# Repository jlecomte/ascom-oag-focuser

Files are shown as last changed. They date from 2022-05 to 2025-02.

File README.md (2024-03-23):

# ASCOM-Compatible OAG Focuser

I do not charge anything to create and maintain these open-source projects. But if you would like to say "thanks" for this project, feel free to send any amount through Paypal using the button below. I appreciate your support!

(https://www.paypal.com/donate/?hosted_button_id=49UXY8F6VVYFA)

<!-- toc -->

- [Introduction](#introduction)
  * [Is This For You?](#is-this-for-you)
  * [Use As A Standalone Focuser](#use-as-a-standalone-focuser)
- [Finished Product](#finished-product)
- [Demo](#demo)
- [Pre-Requisites](#pre-requisites)
- [Hardware / BOM](#hardware--bom)
- [ASCOM Driver](#ascom-driver)
  * [Downloading And Installing The Driver](#downloading-and-installing-the-driver)
  * [Compiling The Driver (For Developers Only)](#compiling-the-driver-for-developers-only)
  * [Screenshots](#screenshots)
- [Standalone Focuser Application](#standalone-focuser-application)
- [Arduino Firmware](#arduino-firmware)
  * [Microcontroller Compatibility](#microcontroller-compatibility)
  * [Compiling And Uploading The Firmware](#compiling-and-uploading-the-firmware)
- [Electronic Circuit](#electronic-circuit)
- [Mechanical Components](#mechanical-components)
  * [OAG Compatibility](#oag-compatibility)
  * [Gear And Pinion](#gear-and-pinion)
- [Calibration Procedure](#calibration-procedure)
- [Troubleshooting](#troubleshooting)
- [Frequently Asked Questions (FAQ)](#frequently-asked-questions-faq)
- [Credits](#credits)

<!-- tocstop -->

## Introduction

Shortly after I got started in astrophotography, I noticed that the stars in my images were slightly elongated due to some differential flexure somewhere in my imaging system (see [Cloudy Nights thread](https://www.cloudynights.com/topic/775260-good-guiding-but-elongated-stars-along-e-w-direction/) — I strongly suspect that it is sag in my focuser...) The permanent solution was to switch from using a guide scope to using an off-axis guider (OAG) and that immediately resolved my issue. Now, my stars are perfectly round, which is great! For reference, I purchased the [ZWO OAG](https://astronomy-imaging-camera.com/product/zwo-oag) and the accompanying [ZWO 1.25" helical focuser](https://astronomy-imaging-camera.com/product/zwo-1-25%E2%80%B3-helical-focuser).

As good as this sounds, the OAG brought a number of new challenges which I did not have to deal with before. First, when using an OAG, the field of view is very small, which sometimes makes it difficult for the guiding software to detect guide stars. Second, the OAG requires some amount of refocusing when switching filters. Indeed, filters are not always parfocal. Most importantly, a refractor (even an apochromatic triplet...) will focus various wavelengths at different distances, and this is the primary reason why it is required to change the focus of the main imaging camera (using filter offsets) when changing filters. Unfortunately, while the imaging sensor is located _behind_ the filter wheel, the OAG is always placed _before_ the filter wheel (Otherwise, especially when using narrowband filters, you would not be able to find a single guide star... Also, placing the filter wheel further away from the imaging sensor would cause vignetting...) and this is why, under specific conditions (see "Is this For You" paragraph below), the guide camera might show out-of-focus images while the imaging camera is in focus, and even though the guide camera was independently focused while another filter was selected in the filter wheel.

While guiding software like PHD2 can accommodate slightly out-of-focus guide stars by computing their centroid, out-of-focus guide images can contain a drastically lower number of detected guide stars, and those that are detected will have a much lower Signal to Noise Ratio (SNR), further reducing the accuracy of the centroid computation. In some situations, PHD2 may not even be able to detect a single guide star, and guiding will be impossible. This has happened to me in the past, and I was forced to _manually_ refocus the guide camera (independently of the main imaging camera of course, using the OAG helical focuser)

Manually refocusing the guide camera throughout the night is not exactly one of the most enjoyable parts of the hobby, so I looked for ways to automate that. Pegasus Astro sells a motorized OAG named [SCOPS OAG](https://pegasusastro.com/products/scops-oag/). However, it is a little expensive for me ($750 US — although it is a really great looking unit!) Furthermore, I discussed with the [N.I.N.A.](https://nighttime-imaging.eu/) developers on their [Discord server](https://discord.gg/fwpmHU4). Since N.I.N.A. can only connect to a single focuser at a time, there is no good solution yet to deal with SCOPS OAG. It is certainly possible to run a second instance of N.I.N.A. that connects to both SCOPS OAG and the guide camera, but there is no way to have those two N.I.N.A. instances communicate to do something upon filter change.

All of this has led me to design and build my own solution to this problem. In this repository, you will find everything you need to motorize and automatically control the ZWO OAG (list of parts, 3D model, electronic schematics, Arduino firmware, ASCOM driver, standalone ASCOM client application, instructions, etc.) I hope you consider building this project if you find yourself in a similar situation. Please note that the ASCOM driver can be used with SCOPS OAG, there is nothing in the Filter Wheel Proxy implementation that is specific to my device.

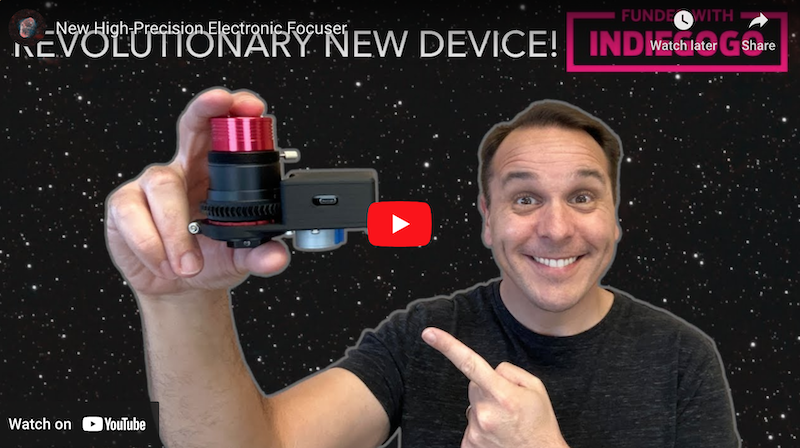
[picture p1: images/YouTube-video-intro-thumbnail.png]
YouTube Intro Video (https://www.youtube.com/watch?v=GP4CpIjJSqA)


### Is This For You?

Not necessarily! It really depends on a lot of factors. For example, if you are using a mirrored telescope, i.e. not a refractor, and if all of your filters come from the same set, e.g., Antlia LRGB filter set, and the filter manufacturer claims they are parfocal, then you may not need this at all because the difference in focus between filters will be so minuscule, you probably won't need to worry about it. However, if you are using a refractor (even an APO triplet), or if you use filters that are not parfocal, you _may_ need this. The only way to find out is to focus your main imaging camera, and then, assuming that you've already defined your filter offsets, go through every single filter in your filter wheel. After every filter change, your imaging application will adjust the focus of your imaging train slightly depending on the filter offset you have defined for the selected filter, and you should look at the image coming out of your guide camera in PHD2. In my case, the stars in my guide camera can be pinpoint when I am using my Luminance filter, but they are large disks when I am on some other filter. That is how you know that this device can be useful for you. This definitely is not for everybody, but the people who have the problem I just described did not really have a good solution until now.

### Use As A Standalone Focuser

Please note that you can use this device, and the accompanying software, to motorize any helical focuser, regardless of how you use that focuser. For example, you could use it to control the focus of a guide scope or even an entire imaging train! Some people have used this project to motorize the focus of a spectrograph. Just remember that if you have a helical focuser that is not from ZWO, you may need to make a few adjustments to the 3D model...

## Finished Product

Here is what the finished product looks like:

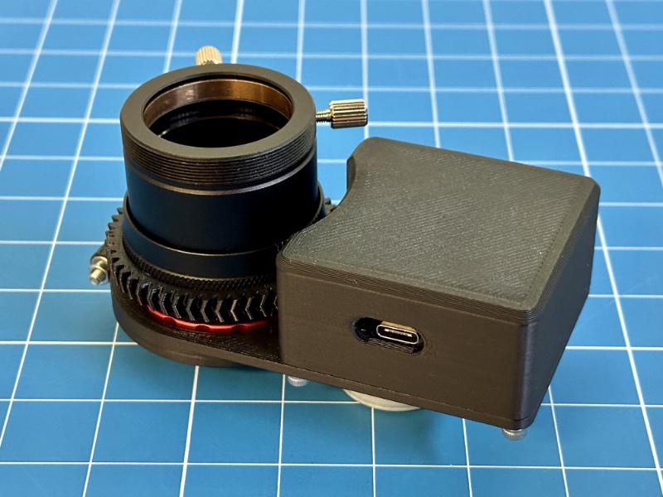
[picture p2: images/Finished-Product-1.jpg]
Finished Product


And here it is, attached to the ZWO OAG, and fitted with a guide camera:

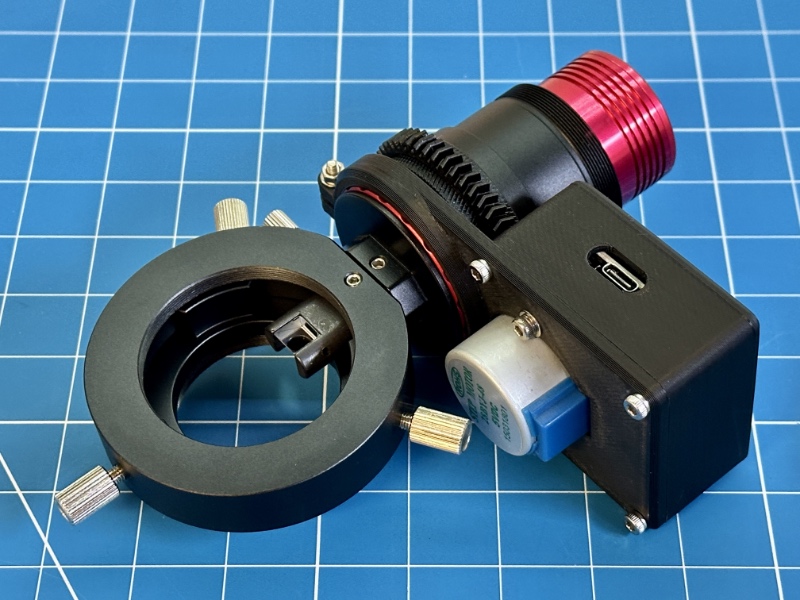
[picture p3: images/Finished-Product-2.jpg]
Finished Product


## Demo

Here is a demo of the system when attached to my telescope, and used as an OAG focuser:

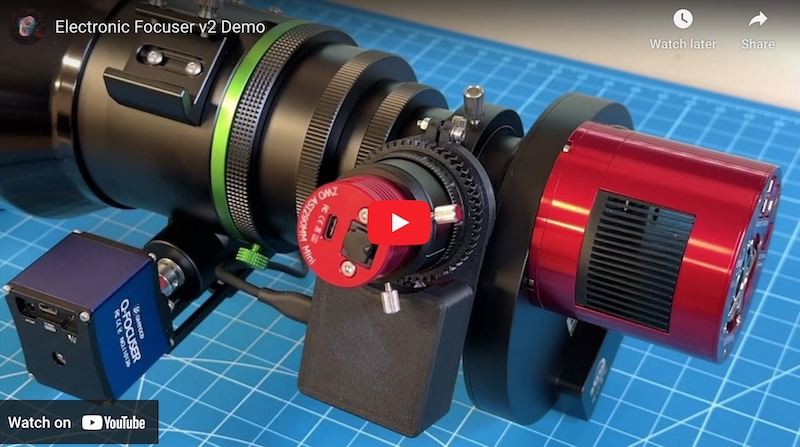
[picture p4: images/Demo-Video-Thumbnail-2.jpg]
YouTube video showing the focuser in action (https://youtu.be/1_InWRwgoRc)


The following video shows what the guide camera sees with and without the OAG focuser upon switching to a different filter:

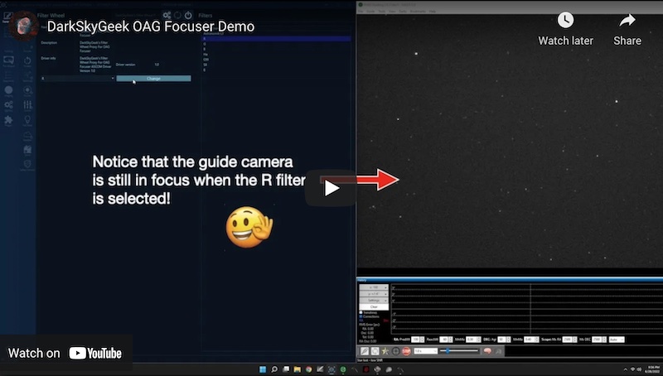
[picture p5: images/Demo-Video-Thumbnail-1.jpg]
YouTube video showing what the guide camera sees with and without an OAG focuser (https://youtu.be/gUapuzT75Z0)


## Pre-Requisites

* A Windows computer (Windows 10 or newer)
* [Microsoft Visual Studio](https://visualstudio.microsoft.com/) (FYI, I used the 2022 edition...)
* [ASCOM Platform](https://ascom-standards.org/)
* [ASCOM Platform Developer Components](https://ascom-standards.org/COMDeveloper/Index.htm)
* [Arduino IDE](https://www.arduino.cc/en/software)
* [FreeCAD](https://www.freecadweb.org/), a free and open-source 3D parametric modeler
* A 3D printer able to print PETG, and a slicer (I use a heavily upgraded Creality Ender 3 v2, and Ultimaker Cura)
* A few basic tools that any tinkerer must own, such as a breadboard, a soldering iron, etc.

## Hardware / BOM

* [ZWO 1.25" helical focuser](https://bit.ly/47JOTRL) or equivalent.
* Arduino-compatible microcontroller board with built-in EEPROM support. I used an [Arduino Nano clone with a USB-C connector (~$10 USD on Amazon for a pack of 3...)](https://www.amazon.com/dp/B09DKHWSY9?tag=darkskygeek-20)
* [ULN2003 Darlington transistor array](https://www.amazon.com/dp/B0CBM23ZJ3?tag=darkskygeek-20) to control the stepper motor using the Arduino's digital I/O pins.
* [28BYJ-48 stepper motor (5V)](https://www.amazon.com/dp/B01CP18J4A?tag=darkskygeek-20)
* [LEDs](https://www.amazon.com/dp/B09XDMJ6KY?tag=darkskygeek-20) and [resistors](https://www.amazon.com/dp/B08FD1XVL6?tag=darkskygeek-20) — These are not required, but they can be useful to debug the firmware while prototyping.
* Connectors — I used [JST-XH connectors](https://www.amazon.com/dp/B01MCZE2HM?tag=darkskygeek-20), only because I already had a bunch of them, along with [a crimping tool](https://www.amazon.com/dp/B078WNZ9FW?tag=darkskygeek-20).
* [Capacitors](https://www.amazon.com/dp/B07PBQXQNQ?tag=darkskygeek-20) — Any 10 to 20µF cpacitor should work (this is just a bulk capacitor, so the exact value does not matter)
* [M2 Threaded Inserts](https://www.amazon.com/dp/B0B8GN63S2?tag=darkskygeek-20)
* [M3 Threaded Inserts](https://www.amazon.com/dp/B0BQJ6CRNJ?tag=darkskygeek-20)

## ASCOM Driver

### Downloading And Installing The Driver

Starting with version `1.0.5`, you can install the ASCOM driver, as well as the standalone focuser control application, by running the executable setup file that you will find in the [releases page](https://github.com/jlecomte/ascom-oag-focuser/releases). By default, it places files under `C:\Program Files (x86)\Dark Sky Geek\OAG Focuser ASCOM Driver`.

### Compiling The Driver (For Developers Only)

Open Microsoft Visual Studio as an administrator (right-click on the Microsoft Visual Studio shortcut, and select "Run as administrator"). This is required because when building the code, by default, Microsoft Visual Studio will register the compiled COM components, and this operation requires special privileges (Note: This is something you can disable in the project settings...) Then, open the solution (`ASCOM_Driver\ASCOM.DarkSkyGeek.OAGFocuser.sln`), change the solution configuration to `Release` (in the toolbar), open the `Build` menu, and click on `Build Solution`. As long as you have properly installed all the required dependencies, the build should succeed and the ASCOM driver will be registered on your system. The binary file generated will be `ASCOM_Driver\bin\Release\ASCOM.DarkSkyGeek.OAGFocuser.dll`. You may also download this file from the [Releases page](https://github.com/jlecomte/ascom-oag-focuser/releases).

### Screenshots

The ASCOM driver registers two new components: `ASCOM.DarkSkyGeek.FilterWheelProxy`, which implements the `IFilterWheelV2` ASCOM interface, and `ASCOM.DarkSkyGeek.OAGFocuser`, which implements the `IFocuserV3` ASCOM interface. Both components have their own settings dialog. Here is what the filter wheel settings dialog looks like:

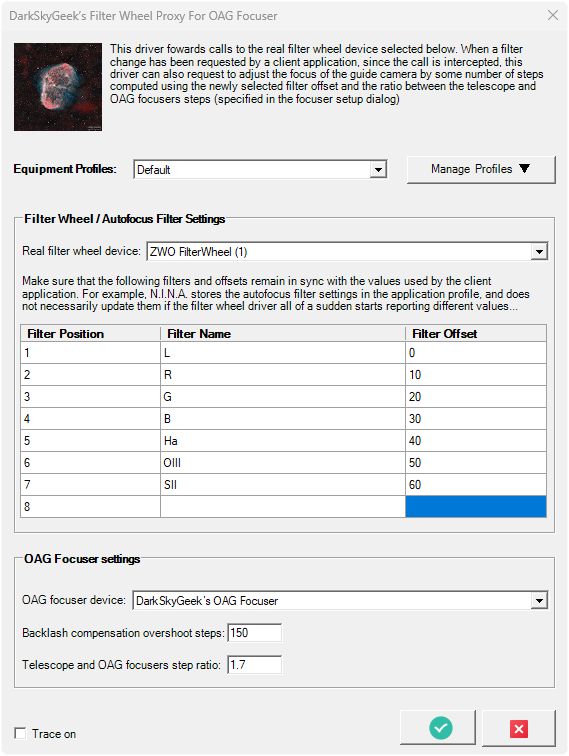
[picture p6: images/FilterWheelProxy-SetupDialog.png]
Filter Wheel Settings Dialog


And here is what the focuser settings dialog looks like:

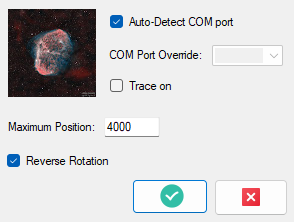
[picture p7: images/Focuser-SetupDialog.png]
Focuser Settings Dialog


## Standalone Focuser Application

Open the `Focuser_App\ASCOM.DarkSkyGeek.FocuserApp.sln` solution in Microsoft Visual Studio, change the solution configuration to `Release` (in the toolbar), open the `Build` menu, and click on `Build Solution`. Very simple! The binary file generated will be `Focuser_App\bin\Release\ASCOM.DarkSkyGeek.FocuserApp.exe`. You may also download this file from the [Releases page](https://github.com/jlecomte/ascom-oag-focuser/releases). Here is what that little standalone application looks like:

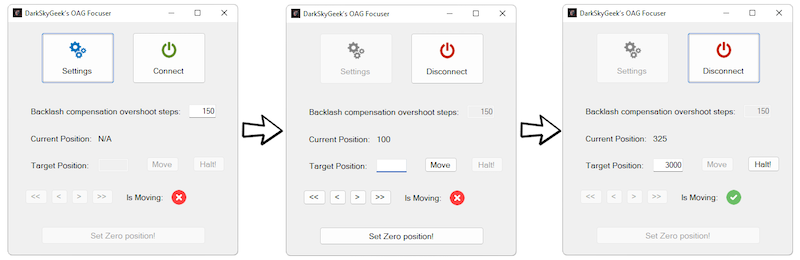
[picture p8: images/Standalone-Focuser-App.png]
Standalone Focuser Control Application


This application allows you to connect to and control DarkSkyGeek’s OAG focuser, and in particular, it enables you to test various backlash compensation values as well as set the zero position. If you use a SCOPS OAG, I can only assume that it came with its own standalone application with similar functionality...

## Arduino Firmware

### Microcontroller Compatibility

All Arduino-compatible microcontrollers that have a **built-in EEPROM** should work. Unfortunately, this excludes the popular [Seeeduino XIAO](https://www.seeedstudio.com/Seeeduino-XIAO-Arduino-Microcontroller-SAMD21-Cortex-M0+-p-4426.html) (one of my favorite microcontroller boards for hobby projects...) If you insist on using a unit that does not have a built-in EEPROM, you will have to customize the firmware to fit your needs. You could technically use a separate EEPROM chip, or you could use the [`FlashStorage` library](https://github.com/cmaglie/FlashStorage) or the [`FlashStorage_SAMD` library](https://github.com/khoih-prog/FlashStorage_SAMD), or you could simply disable the EEPROM code (in which case the device will not remember its last position after a power cycle...) There are quite a few options to choose from, but I recommend using something like an Arduino Nano for example, which is small, affordable, and has everything you need.

**Note:** I tried several Arduino nano clones, and they do not all work. Some of them seem to work, but not reliably. I did not investigate too deeply, but I think it is because their BOD (Brown Out Detection) levels are set too low. When the motor turns, the voltage used to power the microcontroller will drop slightly, and if it drop below a certain level, some units will simply reset themselves in an act of self-protection. So, I strongly recommend the unit linked above, in the BOM list.

### Compiling And Uploading The Firmware

* If needed, add support for the board that you are using in your project.
* You may want to customize the name of the device when connected to your computer. To do that, you will have to update the appropriate `usb_product` key in the appropriate `boards.txt` file... I cannot give you specific instructions for that because they depend on the exact board you are using.
* Finally, connect your board to your computer using a USB cable, open the sketch file located at `Arduino_Firmware\Arduino_Firmware.ino`, and click on the `Upload` button in the toolbar.

## Electronic Circuit

The electronics circuit is fairly straightforward. I included a Fritzing file in the `Electronics/` folder. Here are the schematics:

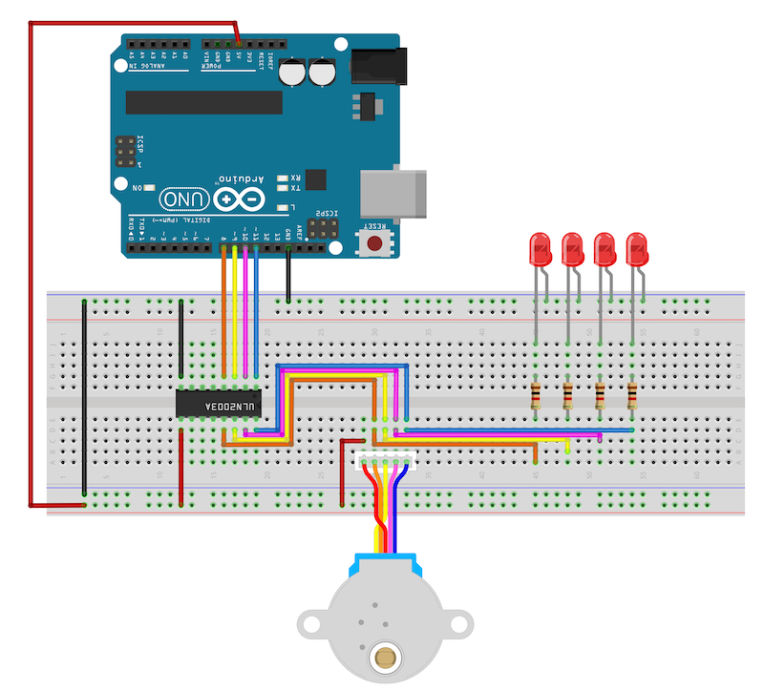
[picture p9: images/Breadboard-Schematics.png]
Breadboard Schematics


Here is what the prototype circuit looks like:

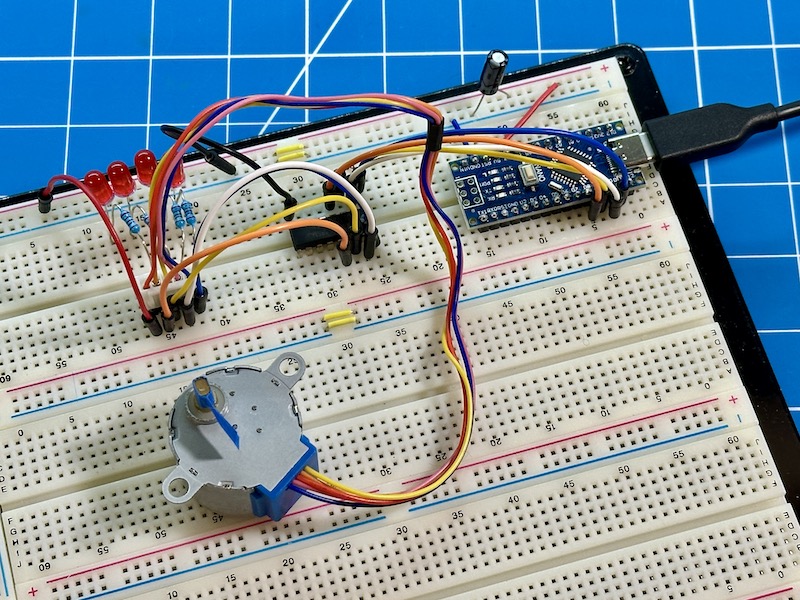
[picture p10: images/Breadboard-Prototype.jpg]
Breadboard Prototype


Here is what the PCB looks like when rendered in KiCad:

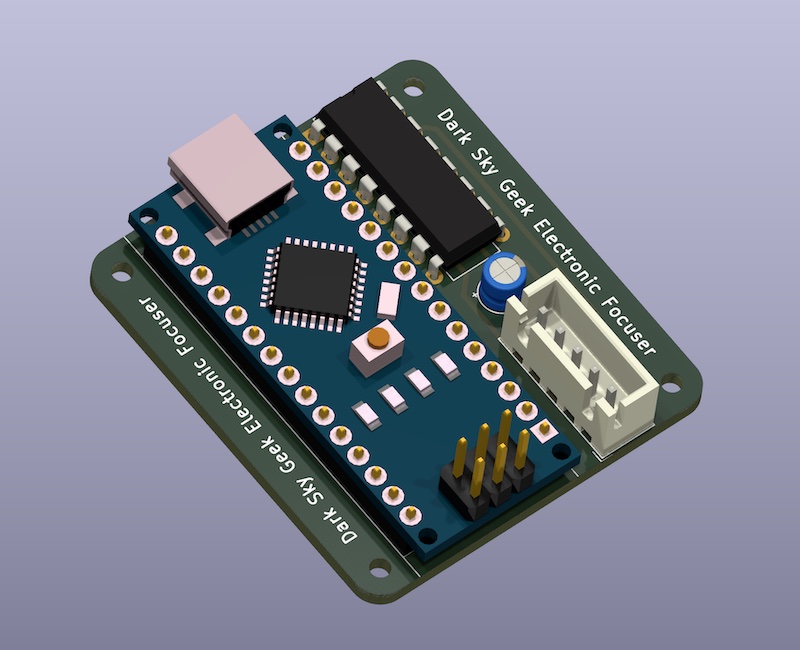
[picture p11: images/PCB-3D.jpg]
Circuit Board 3D Rendered in KiCad


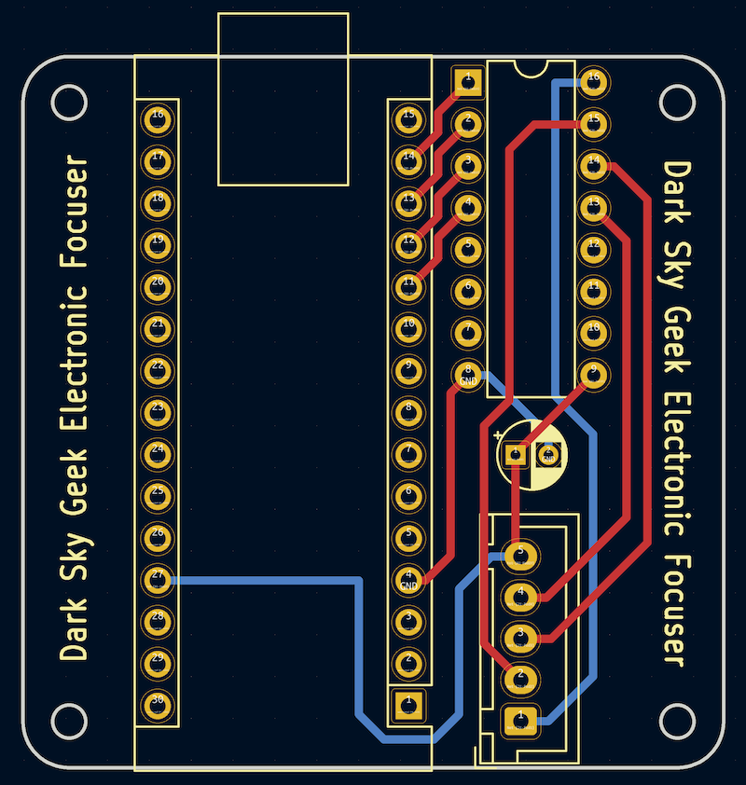
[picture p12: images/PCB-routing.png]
PCB Routing


Here is what the real PCB looks like:

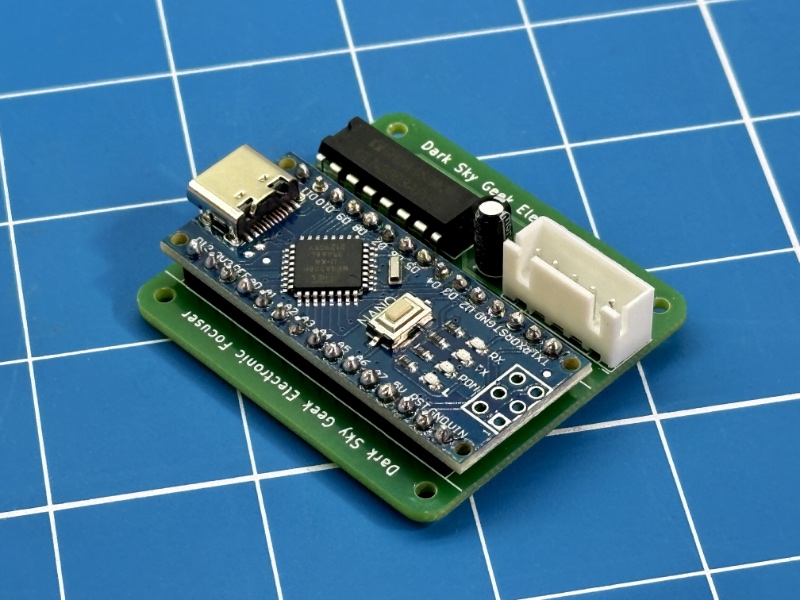
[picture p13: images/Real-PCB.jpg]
Final Circuit Board Top


## Mechanical Components

### OAG Compatibility

In case you are planning to use this electronic focuser with an OAG, please note that [the standard version](3D_Files/Standard-Version/) is compatible (out of the box) with the following OAGs:

* ✅ **ZWO OAG** (standard version)
* ✅ **ZWO OAG-L** (large version) via [this adapter](3D_Files/ZWO-OAG-L/Adapter.FCStd).
* ✅ **Askar OAG**
* ✅ **Player One OAG** (MIN or MAX)

Additionally, an OpenSCAD model designed for the **Celestron OAG** was generously provided by [Endymion42](https://github.com/Endymion42). For more information and photographs, please refer to [this GitHub issue](https://github.com/jlecomte/ascom-oag-focuser/issues/10). The files can be found [here](3D_Files/Celestron-OAG/). **Important note: I will not provide any support whatsoever for this version, so use at your own risk!**

And finally, please note that this electronic focuser is NOT compatible with the following OAGs (at least not without a significant design change):

* 🛑 **QHY OAG**
* 🛑 **Touptek OAG**
* 🛑 **OGMA OAG** — The helical focuser cannot be removed, so you would have to slightly tweak the design of this project to make it fit.
* 🛑 **Antlia OAG** — The helical focuser can be detached from that unit, exposing an M42 male thread, so you would think it might work. However, due to the square OAG body, the stepper motor gets in the way. In my design, the stepper motor sticks out under the body of the electronic focuser to minimize the space the entire unit takes when used with a round OAG. **Note:** Some people have successfully adapted my design to flip the motor around and make it work with this unit.

### Gear And Pinion

In [the first version of this project](https://github.com/jlecomte/ascom-oag-focuser/tree/v1), I was using helical gears. However, this was not a very smart choice because the axial force that results from this design, and the fact that the stepper motor shaft has a bit of longitudinal play caused the backlash to be a bit higher than I would have liked. While it still worked well (thanks to backlash compensation), this new version uses a herringbone pattern for the gear and pinion:

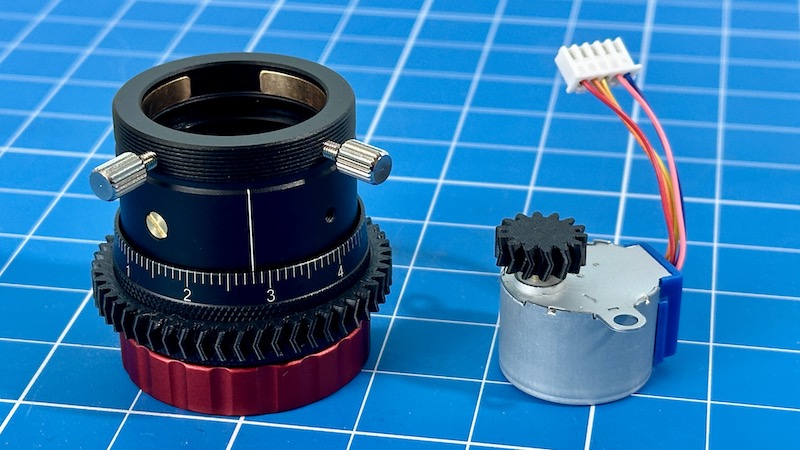
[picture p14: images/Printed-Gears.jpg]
Focuser Gear


It turns out that gears are easy to make on a 3D printer, and work flawlessly. However, here are a few tips I found useful:

* Dry your filament to reduce problems, specifically stringing to a minimum
* Use the proper Z offset, and (if needed) set the initial layer horizontal expansion value in Cura to a negative number, e.g., -0.2mm. It is critical to prevent the dreaded "elephant's foot" (squishing of the first layer)
* To ensure that the first layer adheres well, clean your build plate (I use denatured alcohol)

Another trick that also helped get great results was to slightly loosen the focuser (there are 4 tiny set screws on the ZWO focuser that you can loosen _ever so slightly_ to make it easier to rotate the knurled knob) because these small stepper motors don't have that much torque...

The focuser gear slips onto the knurled knob of the helical focuser. The pinion slips onto the motor shaft, although it might require a light hammer blow to get it fully seated. It is not necessary to use any glue to keep the gears in place.

## Calibration Procedure

Before you can use this device, you have to calibrate it. Here is the procedure:

1. **Filter Offsets Measurement**

   Measuring filter offsets is something you have probably already done because it allows you to run an autofocus routine using your luminance (L) filter, which can be done with very short exposures, thereby saving a lot of time (it is also more accurate). Enter the filter offsets in your imaging application, e.g., N.I.N.A., as well as in the settings dialog of the `DarkSkyGeek’s Filter Wheel Proxy For OAG Focuser` ASCOM device (see screenshot above). Remember that it is critical that your imaging application and the driver have the same filter offset values!

   **Note:** If you measure your filter offsets with a reducer, they will be different. Don't worry about that. Do the entire calibration procedure with your standard astrophotography setup. Once properly set up, the OAG focuser configuration will not need to change whether or not you add a reducer to your imaging train.

2. **Backlash Measurement**

   There are many sources of backlash in this system. The stepper motor itself, due to its internal gearbox, already has some amount of backlash. The 3D printed gear and pinion also have some backlash. And finally, the helical focuser has some backlash as well. All of those sources combine. Thankfully, compensating for backlash is easy and supported by the software in this repository. The trick is to first measure the amount of backlash in your system. That is done using a dial gauge. Please refer to the video below for more details.

   Using the standalone focuser control application, setting a backlash compensation of 0, move in one direction by a large amount. Then, repetitively move in small increments in the opposite direction until the dial indicator starts moving. In my setup, I have a total of about 60 steps of backlash, so I set the backlash compensation amount to 150 (the software uses the so-called "overshoot" backlash compensation method) and it works absolutely flawlessly! Enter the value of the backlash, in number of steps (150 in my case), in the settings dialog of the `DarkSkyGeek’s Filter Wheel Proxy For OAG Focuser` ASCOM device (see screenshot above)

3. **Zero Position**

   Manually rotate the OAG focuser until it hits its mechanical zero position. Connect the OAG focuser to a computer (assuming you had previously installed the OAG focuser ASCOM driver on that computer), open the standalone focuser app, connect to the device, and click on the "Set Zero position!" button.

4. **Steps Ratio Measurement**

   The "steps ratio" allows the Filter Wheel Proxy ASCOM driver to answer the following question: Upon filter change, the main focuser has to move n steps in this direction. How many steps does the OAG focuser need to move, and in which direction?

   The best way to measure the steps ratio is to use 2 instances of N.I.N.A. The first instance is connected to the telescope focuser and the main imaging camera. The second instance is connected to the OAG focuser and the guide camera. Then, follow these steps:

   * Run an autofocus routine in both N.I.N.A. instances (start with the one that controls the telescope focuser and the main imaging camera)
   * Take note of the position of the OAG focuser.
   * Move the telescope focuser by, for example, 300 steps outward.
   * Run another autofocus routine on the second N.I.N.A. instance (the one that controls the OAG focuser and the guide camera)
   * Subtract the new position of the OAG focuser with the initial position, and divide that number by the number of steps you moved the main telescope focuser (300 in our example). That will give you the steps ratio. Note that this will be a negative number. In my case, the steps ratio is -2.64.
   * You can run the autofocus routine several times, and average the positions obtained to increase accuracy.
   * Enter the steps ratio in the settings dialog of the `DarkSkyGeek’s Filter Wheel Proxy For OAG Focuser` ASCOM device (see screenshot above)

5. **Test**

   Once you have calibrated the OAG Focuser, you can close the second instance of N.I.N.A. and open PHD2. Use the first instance of N.I.N.A. as you normally would, although instead of connecting your filter wheel directly, you will connect to the `DarkSkyGeek’s Filter Wheel Proxy For OAG Focuser` device. Looking at the PHD2 live view, change the filter in the filter wheel and watch the PHD2 live view becoming blurry and then sharp again, automatically! Isn't technology beautiful?!

This procedure is explained in great detail in the following video:

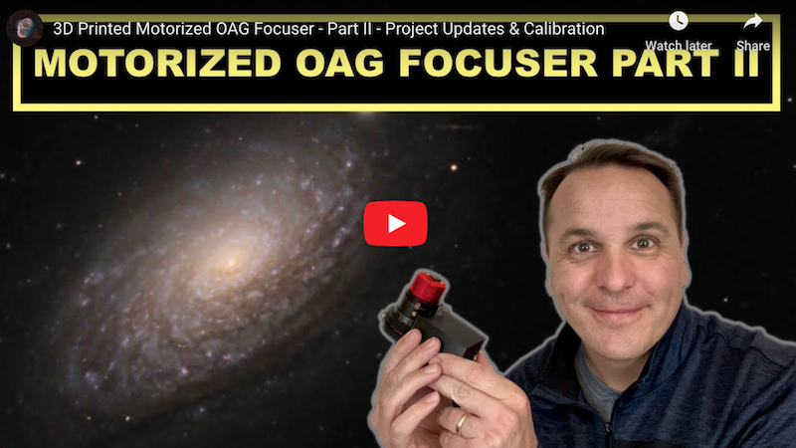
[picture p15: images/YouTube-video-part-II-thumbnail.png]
YouTube video explaining how to properly calibrate this device (https://www.youtube.com/watch?v=zPPIgVuxk4Y)


## Troubleshooting

**The standalone focuser application is not able to connect to the device**

**Step 1:** On Windows, open the Device Manager, and expand the `Ports (COM & LPT)` section. Connect the Arduino. You should see a new COM port appear. If you don't, there is a problem with Windows, the Arduino, or the USB cable.

**Step 2:** Assuming that a new COM port appeared in step 1, open the driver settings dialog from the standalone focuser application, and ensure that you have the `Auto-Detect COM port` option enabled.

**Step 3:** Make sure that no other application is currently using the COM port assigned to the device. On Windows, a single process can be connected to a COM port at any given time, so if you happen to be running the Arduino IDE (for example) at the same time, it will have likely automatically connected to the Arduino via the COM port, and the standalone focuser application will not be able to connect.

**Step 4:** If all else fails, look for the driver logs under `<DOCUMENTS FOLDER>\ASCOM\Logs <DATE>\` and open the most recent file. Feel free to open an issue, and paste the content of the log file.

**The focuser turns in the wrong direction**

Depending on how you wire the stepper motor, it may turn in different directions. This is especially important when you first try the device, because its position is set to 0 by default and the driver will throw an error if the position becomes negative. So if you encounter an error on first try, don't worry! Disconnect the focuser in the application (no need to disconnect the USB cable...), open the focuser settings dialog, toggle the "Reverse Rotation" option (see screenshot above), and click OK. Then, connect to the focuser and try again.

## Frequently Asked Questions (FAQ)

**I built this project and it does not work, can you help?**

_Maybe. As indicated in the `LICENSE` file, I do not provide any official guarantee or support. That being said, if you open a GitHub issue in this repository and ask nicely, I will likely respond. Just make sure that you provide all the necessary details so that I understand what the issue might be. While on that note, keep in mind that troubleshooting an issue on your own is by far the best way to learn new things._

**Why did you not use the `Stepper` or `AccelStepper` library in the Arduino firmware?**

_It might seem strange that I decided to "manually" control the stepper motor instead of using the standard [`Stepper` library](https://www.arduino.cc/reference/en/libraries/stepper/) or the popular [`AccelStepper` library](https://www.arduino.cc/reference/en/libraries/accelstepper/). There are two reasons for that:_

1. _I need to be able to handle incoming requests while the motor is moving, e.g., `COMMAND:FOCUSER:ISMOVING` or `COMMAND:FOCUSER:HALT`. This is not possible with any of the aforementioned libraries._
2. _To save power, to prevent heat buildup, and to eliminate vibrations, I de-energize the stepper motor by setting all the pins to LOW once it has reached the desired position. This is also not supported by any of the aforementioned libraries, and it makes a huge difference! If you don't believe me, try commenting out that part of the code, and play with the firmware for a little while (you don't even need to actively move the motor). Then, feel how hot the motor gets... Also, feel how much the motor vibrates while energized, and consider the impact that might have on your images..._

**Why is backlash compensation not implemented in the focuser driver?**

_The software included in this repository (specifically the `FilterWheelProxy` ASCOM component) was designed and implemented so that it may be used with other OAG focusers, including commercial units such as the SCOPS OAG, and I have no idea whether their driver handles backlash compensation. This way, no matter which focuser you use to adjust the focus of your guide camera, as long as its driver implements the standard `IFocuserV3` ASCOM interface, this will work and you will enjoy the benefits of backlash compensation!_

**What is the positional accuracy of this focuser?**

_Using a precision dial indicator (see "Backlash Measurement" section), I was able to measure the positional accuracy of this device (move 1,000 steps in one direction, move 1,000 steps in the opposite direction, and measure the difference between the starting and ending positions). Astoundingly, it is of the order of about 10μm!_

**My antivirus identifies your setup executable file as a malware (some kind of Trojan)**

_This is a false detection, extremely common with installers created with [Inno Setup](https://jrsoftware.org/isinfo.php) because virus and malware authors also use Inno Setup to distribute their malicious payload... Anyway, there isn't much I can do about this, short of signing the executable. Unfortunately, that would require a code signing certificate, which costs money. So, even though the executable I uploaded to GitHub is perfectly safe, use at your own risk!_

## Credits

I would like to thank _Christophe de la Chapelle_ of the popular French-language YouTube channel [La Chaîne Astro](https://www.youtube.com/c/cdlc48) because he gave me the idea to build a focuser for my OAG after he demonstrated how he had built a simple focuser using 3D printed parts and a stepper motor for his telescope.

I would like to also thank _Stefan Berg_, creator of [N.I.N.A.](https://nighttime-imaging.eu/), and _Linwood Ferguson_ (see [his web site](https://www.captivephotons.com/Photography/Astrophotography/)) for giving me the idea to create a "proxy" filter wheel component while discussing the design of this system on the [N.I.N.A. Discord server](https://discord.gg/fwpmHU4).

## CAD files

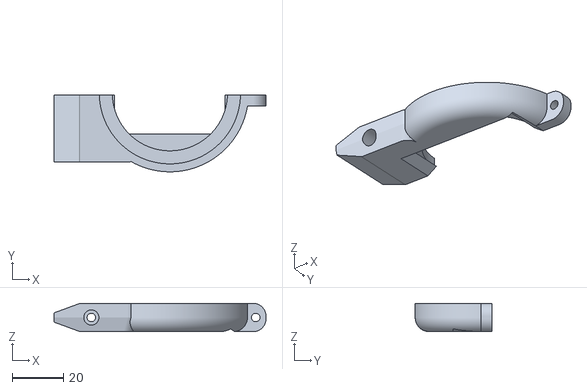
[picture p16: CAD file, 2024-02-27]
3D_Files/Celestron-OAG/STL/BaseA.stl
82.5 x 29.8 x 11.0

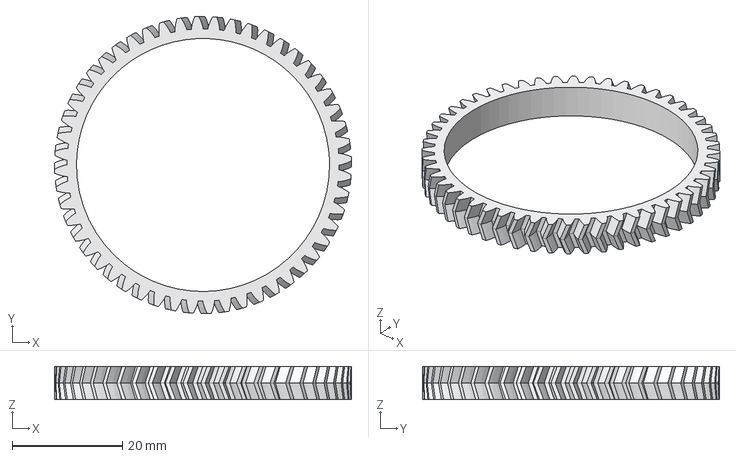
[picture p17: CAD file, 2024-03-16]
3D_Files/Standard-Version/Gears.FCStd
54.0 x 54.0 x 6.00 mm

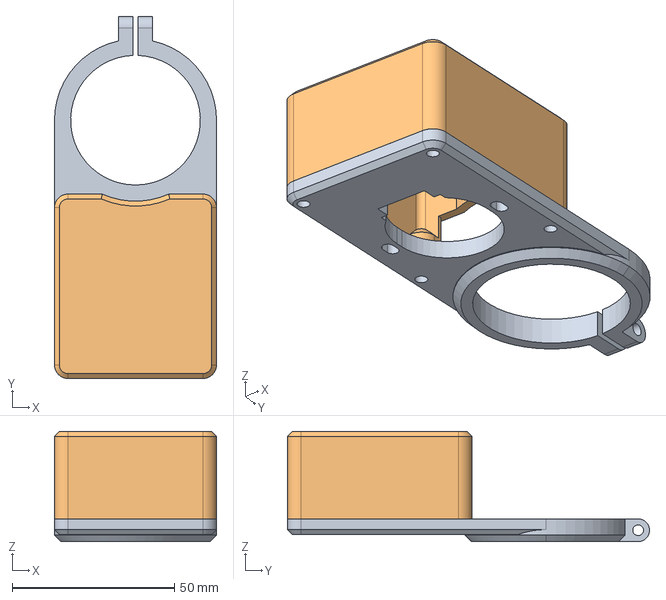
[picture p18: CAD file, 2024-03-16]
3D_Files/ZWO-OAG-L/Body.FCStd
50.0 x 111.7 x 34.0 mm
Base
Cover

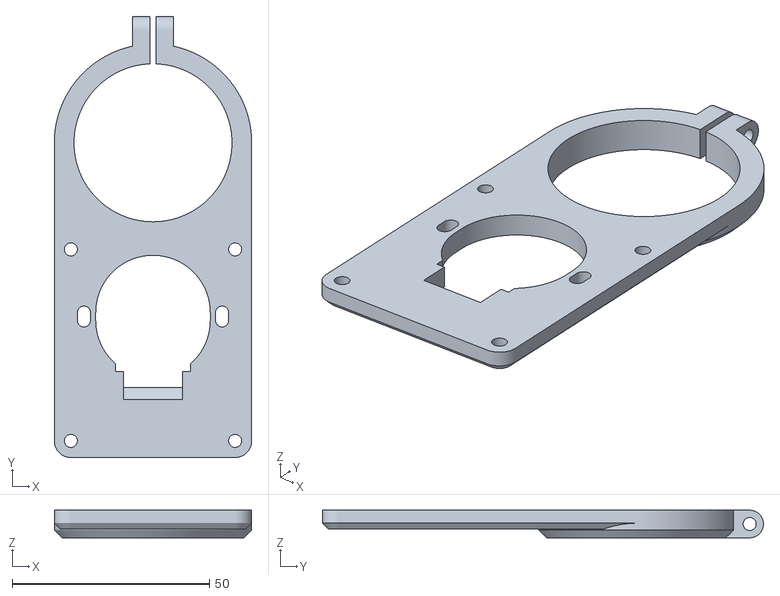
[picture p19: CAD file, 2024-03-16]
3D_Files/ZWO-OAG-L/STL/Base.stl
50.0 x 111.7 x 7.00

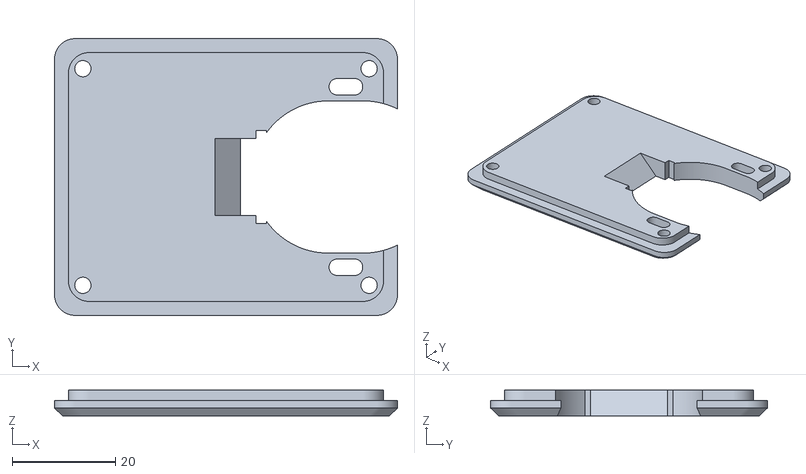
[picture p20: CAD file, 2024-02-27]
3D_Files/Celestron-OAG/STL/CoverPlate.stl
66.5 x 53.7 x 5.00

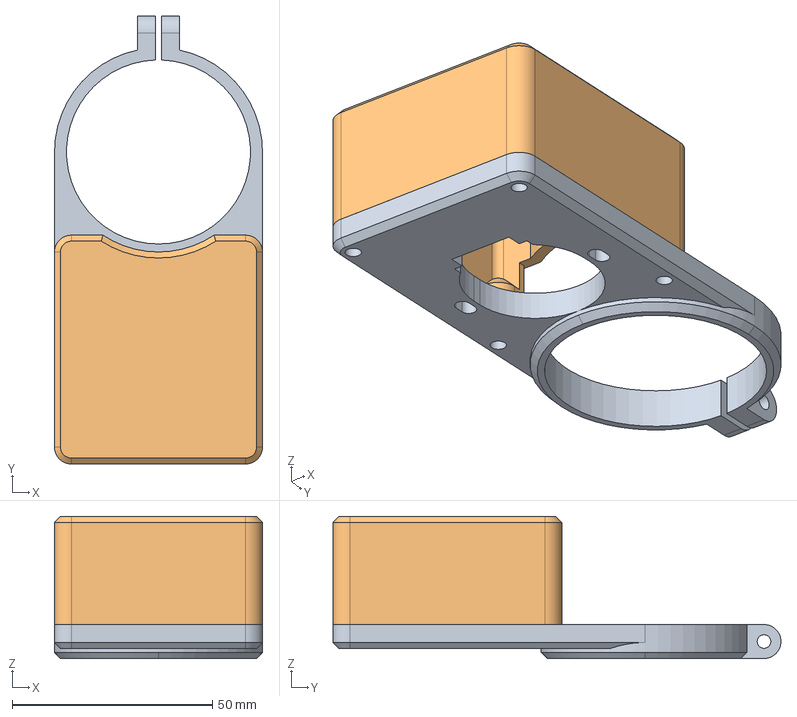
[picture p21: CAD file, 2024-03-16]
3D_Files/Standard-Version/Body.FCStd
52.0 x 112.0 x 35.5 mm
Base
Cover

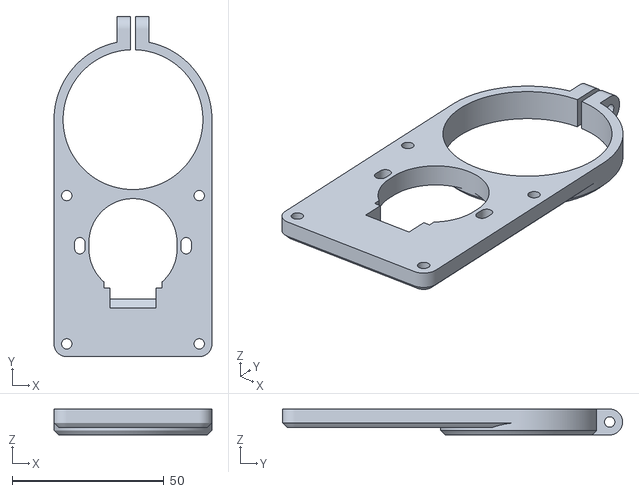
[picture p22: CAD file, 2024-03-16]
3D_Files/Standard-Version/STL/Base.stl
52.0 x 112.0 x 8.50

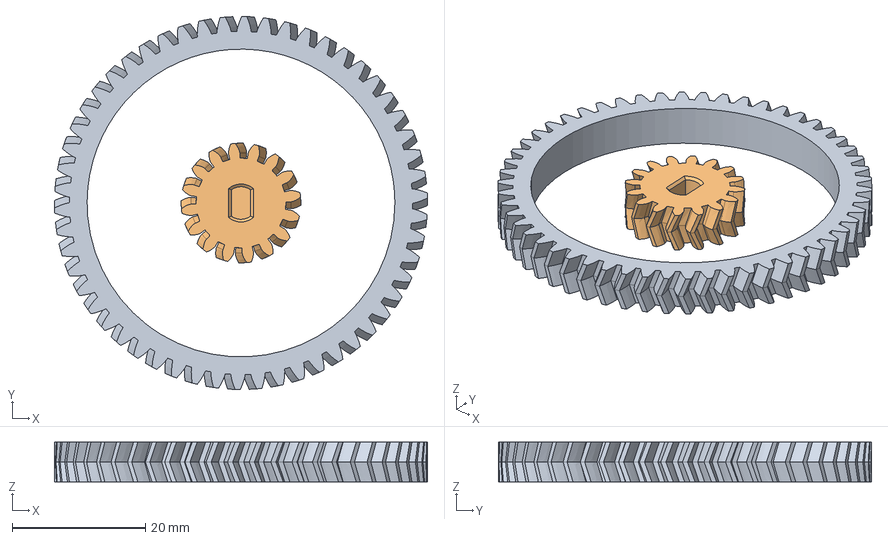
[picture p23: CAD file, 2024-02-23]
3D_Files/ZWO-OAG-L/Gears.FCStd
56.0 x 56.0 x 6.00 mm

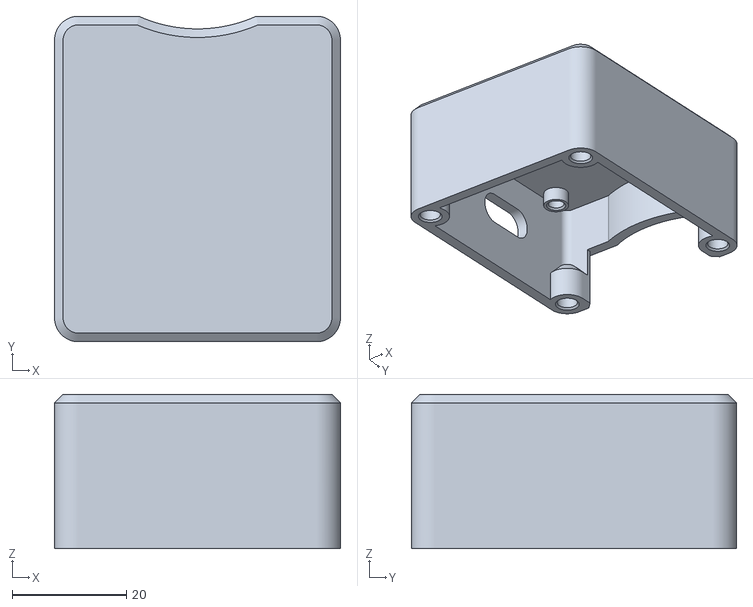
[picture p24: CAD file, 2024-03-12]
3D_Files/ZWO-OAG-L/STL/Cover.stl
50.0 x 56.9 x 27.0

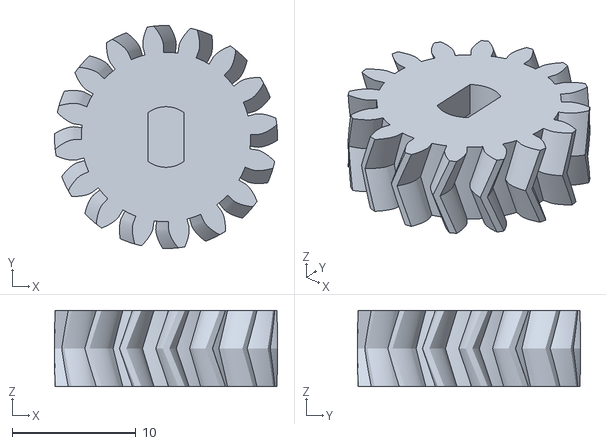
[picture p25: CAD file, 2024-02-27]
3D_Files/Celestron-OAG/STL/Pinion.stl
18.0 x 18.0 x 6.15

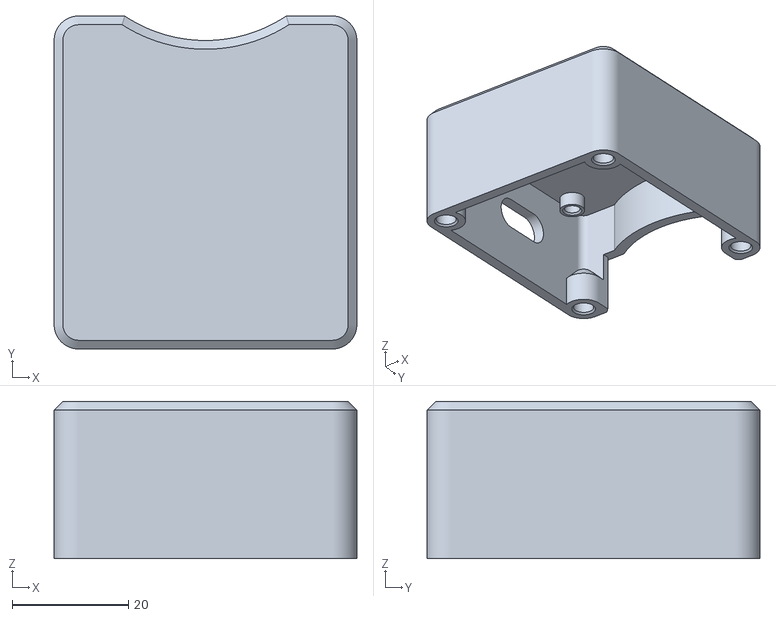
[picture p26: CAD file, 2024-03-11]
3D_Files/Standard-Version/STL/Cover.stl
52.0 x 57.2 x 27.0

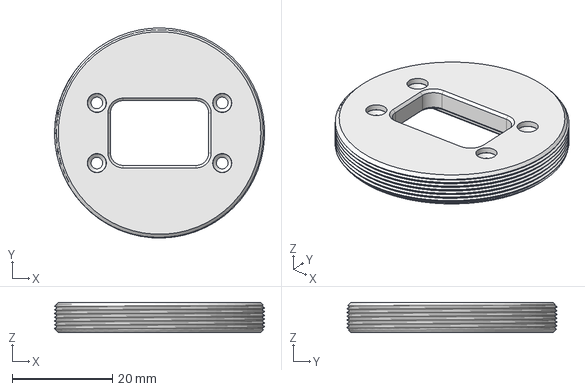
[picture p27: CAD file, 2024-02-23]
3D_Files/ZWO-OAG-L/Adapter.FCStd
41.9 x 41.9 x 6.00 mm

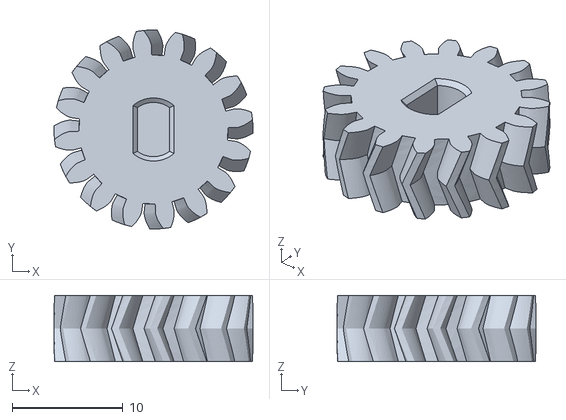
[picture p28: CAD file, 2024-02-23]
3D_Files/ZWO-OAG-L/STL/Pinion.stl
18.0 x 18.0 x 6.00

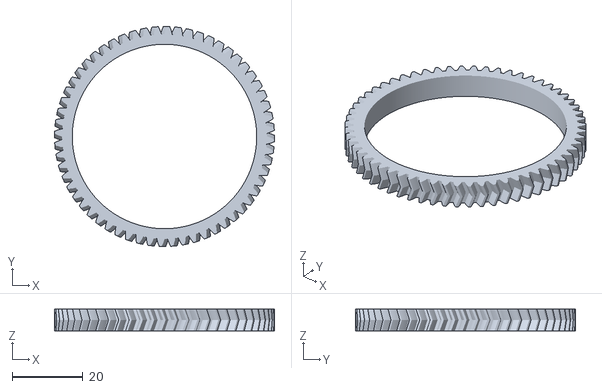
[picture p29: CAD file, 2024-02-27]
3D_Files/Celestron-OAG/STL/Gear.stl
62.0 x 62.0 x 6.15

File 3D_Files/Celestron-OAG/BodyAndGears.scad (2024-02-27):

/*
 * Openscad design for case to use on Celestron OAG for Julien Lecomte's
 * ASCOM-Compatible OAG Focuser
 *
 * Licensed under the MIT License. See the accompanying LICENSE file for terms.
 */


 
 // https://github.com/chrisspen/gears
 // https://github.com/revarbat/BOSL

include <BOSL/constants.scad>
use <BOSL/shapes.scad>
include <gears-master/gears.scad>


$fn=300;
//$fn=20;


// Dimensions for Celestron Base

OAGWidth = 30.6;
OAGLength = 42.8+0.2;
OAGAngle = 45;
OAGOffset = (6.5-5.5)/2;  // The OAG helical is offset from the center of the OAG towards the OTA side
OAGClampAreaHeight = 3.9 - 0.4;
OAGHelicalRotatingShaftDiameter = 51.85;

// Dimensions for Celestron Gear
FudgeFactor = 0.1;
GearInnerDiameter = OAGHelicalRotatingShaftDiameter+FudgeFactor;
GearWidth = 6.15;
NumberOfTeeth = 60;
NumberOfPinionTeeth = 16;

PinionShaftDiameter =4.89;
PinionShaftNotchWidth = 2.9;
PinionShaftDepth = 5;


UpShiftToClearOAG = 5;
BaseExtension = 10;

BaseWidthA = 53.65;
BaseWidthB = 50.5;
BaseSection1Length = 90; // Gets cut off by the clamp hemicircle, just needs to be long enough 
BaseClampRingThickness = 6 + UpShiftToClearOAG;
BaseSection1ThicknessA = BaseClampRingThickness/2;
BaseSection1ThicknessB = BaseClampRingThickness/2;
VerticalLockingSlotLength = 10;
DiagonalSlotLength = sqrt(pow(BaseClampRingThickness/3,2) + pow(VerticalLockingSlotLength,2));
AngleForDiagonalSlot = atan(VerticalLockingSlotLength / (BaseClampRingThickness/3) );

BaseCoverBoltHoleXOffset = 4  +.5 + 1;
BaseCoverBoltHoleXSeparation = 47.5+ BaseExtension - 2;
BaseCoverBoltHoleYSeparation = 45 -1 -2;
BaseCoverInsertOuterDiameter = 7;


GapToHelicalRotatingShaft = 1.5; // How much space around rotating section of helix focus to allow for ring
CelestronClampingAreaTubeDiameter = 42.8;
BaseClampInnerDiameter = 42.8 + 2;
BaseClampWallThickness = BaseWidthA-BaseWidthB; // Doesn't need to be this
BaseClampOuterDiameter = OAGHelicalRotatingShaftDiameter + 2*GapToHelicalRotatingShaft + 2*BaseClampWallThickness;



BaseCornerFillet = 4;
CoverBoltHoleDiameter = 3.15;
CoverBoltInsertDiameter = 3.9;
CoverBoltHoleALength = 7;
CoverBoltHoleBLength = 5;
BoltHoleXAdjust = CoverBoltHoleDiameter*1.5;
CoverWallThickness = 2.5;
CoverWallHeight = 22.5-GearWidth +4.7;  // This is a fudge, manually adjusted
TopCoverThickness = 3;
TopCoverLipThickness = 2;

ClampBoltHoleDiameter = 3.2;
ClampGap = 1.5;
ClampBoltHeadDiameter = 5.4 + .5;
ClampNutWidth = 5.4 + 0.2;
ClampBoltNutHoleDepth = 16;

StepperHoleSpacing = 35;
StepperBoltSlotLength = 4.5 + 2;
StepperBoltSlotWidth = 3.15;
StepperBoltDiameter = 3.1;
SlotFillet = 1.5;
HalfSlotLengthPlay = (StepperBoltSlotLength-StepperBoltDiameter);
StepperShaftOffsetFromCenter=8;

StepperSlot1XOffset = 12;
StepperSlot1Width = 18;
StepperSlot1Length = 2;

StepperSlot2Width = 15;
StepperSlot2LengthTop = 2.7;
StepperSlot2SlopeAngle = 45;
StepperCenterOffsetFromRightEdge =  36.5+10 + BaseExtension;
StepperHoleDiameter = 28 + 1.5;


// Circuit Board Parameters
CircuitBoardHoleHeight = 2.71;
CircuitBoardHoleOuterDiameter = 5.2;
CircuitBoardHoleInnerDiameter = 3.2 + 0.2;
CircuitBoardHoleSeparationX = 37;  // Measured in Prusaslicer
CircuitBoardHoleSeparationY = 37.6;  // Measured in Prusaslicer
CircuitBoardHoleOffsetX = 10; // Offset from X=0 end
//CircuitBoardHoleOffsetY = 5; // Offset from Y=BaseWidthA/2 side;   DECIDED TO CENTER
CircuitBoardSinkIntoPlate = 4;
CircuitBoardUSBHoleXOffsetFromInsert = 23.8; //
CircuitBoardUSBHoleOffsetFromRightEdge = CircuitBoardHoleOffsetX + CircuitBoardUSBHoleXOffsetFromInsert;
CircuitBoardUSBZOffsetFromTopOfInsert = 7;
CircuitBoardUSBZDim = 7;
CircuitBoardUSBXDim = 15;



// Measured off printed parts, not derived and not quite accurate...
//SmallGearDiameter = 16;
SmallGearDiameter = 16 * floor(14*NumberOfTeeth/52)/14;
//LargeGearDiameter = 61.5;
//LargeGearDiameter = 81.5;
LargeGearDiameter = 61.5;
GearOverlap = 1.9;
GearCentersSeparation = (SmallGearDiameter + LargeGearDiameter)/2 - GearOverlap;
echo("GearCentersSeparation = ", GearCentersSeparation);


CelestronLargeSCTDiameter1 = 94.6;
CelestronLargeSCTDiameter2 = 89.2;
CelestronLargeSCTOffsetFromBottom =  11-4.4; // Measured
CelestronLargeSCTInsetFromSide = 15.08 - 11.45 + 1.5;
CelestronLargeSCTRingHeight1 = 11.5;
CelestronLargeSCTRingHeight2 = 2.5;







//rotate([180,0,0])
//CelestronBaseA();
//rotate([180,0,0])
//CelestronBaseB();
//CelestronGear();
//rotate([180,0,0])
translate([0,0,-GearWidth - 6 - TopCoverThickness -4.7])
TopCover();
//CelestronBase();
//CoverBoltHoleCutouts();
//CoverWallSection();
//MotorCutouts();
//DiagonalSlot();
//InsideSlice();

// MakeANut(10,5);
//OAGBlock();
//ClampBoltSection();

//translate([StepperCenterOffsetFromRightEdge+StepperShaftOffsetFromCenter + GearCentersSeparation,0,-GearWidth - 6])
// CelestronGear();

//translate([StepperCenterOffsetFromRightEdge+StepperShaftOffsetFromCenter,0,-GearWidth - 6])
//rotate([0,180,0])
// MotorPinion();

module TopCover() {
     XLengthA = 2*BaseCoverBoltHoleXOffset + BaseCoverBoltHoleXSeparation;
     XLengthB = XLengthA - (BaseWidthA-BaseWidthB);
     mirror([0,0,1]) {
	  difference() {
	       union() {
		    hull() { // Create beveled edge around plate
			 union() {
			      translate([XLengthA/2, 0, TopCoverThickness/4-BaseCornerFillet])
				   difference() {
				   cuboid([XLengthA, BaseWidthA, TopCoverThickness/2+BaseCornerFillet*2], center=true, fillet=BaseCornerFillet, edges = EDGES_Z_ALL);
				   translate([0,0,-TopCoverThickness/2/2-0.0001])
					cube([XLengthA+0.1, BaseWidthA+0.1, BaseCornerFillet*2], center=true);
			      }
			      translate([XLengthA/2, 0, TopCoverThickness/4-BaseCornerFillet+TopCoverThickness/2-0.000001])
				   difference() {
				   cuboid([XLengthB, BaseWidthB, TopCoverThickness/2+BaseCornerFillet*2], center=true, fillet=BaseCornerFillet, edges = EDGES_Z_ALL);
				   translate([0,0,-TopCoverThickness/2/2-0.0001])
					cube([XLengthB+0.1, BaseWidthB+0.1, BaseCornerFillet*2], center=true);         
			      }       

			 }
		    }
		    /* translate([XLengthA/2, 0, TopCoverThickness/4-BaseCornerFillet+TopCoverThickness/2-0.000001]) */
		    /* 	 difference() { */
		    /* 	 cuboid([XLengthB, BaseWidthB, TopCoverLipThickness+BaseCornerFillet*2], center=true, fillet=BaseCornerFillet, edges = EDGES_Z_ALL); */
		    /* 	 translate([0,0,-TopCoverThickness/2/2-0.0001]) */
		    /* 	      cuboid([XLengthB+0.1, BaseWidthB+0.1, BaseCornerFillet*2], center=true, fillet=BaseCornerFillet, edges = EDGES_Z_ALL); */
		    /* } */
		    XLength = 2*BaseCoverBoltHoleXOffset + BaseCoverBoltHoleXSeparation;
		    ZThickness = TopCoverLipThickness + 200;
		    translate([XLengthA/2,0,-TopCoverLipThickness])
			 difference() {
			 translate([0,0,ZThickness/2])
			      cuboid([XLength-2*CoverWallThickness -0.4 , BaseWidthA-2*CoverWallThickness -0.4 , ZThickness], center=true, fillet=BaseCornerFillet, edges = EDGES_Z_ALL);
			 translate([0,0,TopCoverLipThickness + ZThickness/2])
			      cuboid([XLength-2*CoverWallThickness+0.1, BaseWidthA-2*CoverWallThickness+0.1, ZThickness], center=true, fillet=BaseCornerFillet, edges = EDGES_Z_ALL);
		    }

	       }
	       union() {
		    translate([0,0,-6])
			 MotorCutouts();
		    CoverBoltHoleCutouts();
	       }
	  }
     }

}

module CelestronGear() {
     herringbone_gear(modul=1, tooth_number=NumberOfTeeth, width=GearWidth, bore=GearInnerDiameter, pressure_angle=20, helix_angle=20);
}

module MotorPinion() {
     difference() {
	  herringbone_gear(modul=1, tooth_number=NumberOfPinionTeeth, width=GearWidth, bore=0, pressure_angle=20, helix_angle=20);
	  translate([0,0,-0.001])
	  difference() {
	       cylinder(d=PinionShaftDiameter, h=PinionShaftDepth);
	   union() {
	       translate([PinionShaftNotchWidth/2 + 5,0,0])
		    cube([10,10,PinionShaftDepth], center=true);
	       translate([-PinionShaftNotchWidth/2 - 5,0,0])
		    cube([10,10,PinionShaftDepth], center=true);
	  }
     }
     }
}



module CircuitBoardSink() {
     echo("Circuit Board Sink Into Plate = ",CircuitBoardSinkIntoPlate);
     XLength = 2*BaseCoverBoltHoleXOffset + BaseCoverBoltHoleXSeparation - BaseExtension;
     translate([XLength/2, 0, CircuitBoardSinkIntoPlate - 0.01])
	  difference() {
	  translate([0,0,-CoverWallHeight/2])
	       cuboid([XLength-2*CoverWallThickness, BaseWidthA-2*CoverWallThickness, CoverWallHeight], center=true, fillet=BaseCornerFillet, edges = EDGES_Z_ALL);
	  translate([0,0,-CoverWallHeight/2 - CircuitBoardSinkIntoPlate/2 -0.01])
	       cuboid([XLength-2*CoverWallThickness+1, BaseWidthA-2*CoverWallThickness +1, CoverWallHeight-CircuitBoardSinkIntoPlate], center=true, fillet=BaseCornerFillet, edges = EDGES_Z_ALL);
     }
}
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

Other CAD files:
3D_Files/Standard-Version/STL/Gear.stl
3D_Files/Standard-Version/STL/Pinion.stl
3D_Files/ZWO-OAG-L/STL/Gear.stl
3D_Files/Celestron-OAG/STL/BaseB.stl
3D_Files/ZWO-OAG-L/STL/Adapter.stl

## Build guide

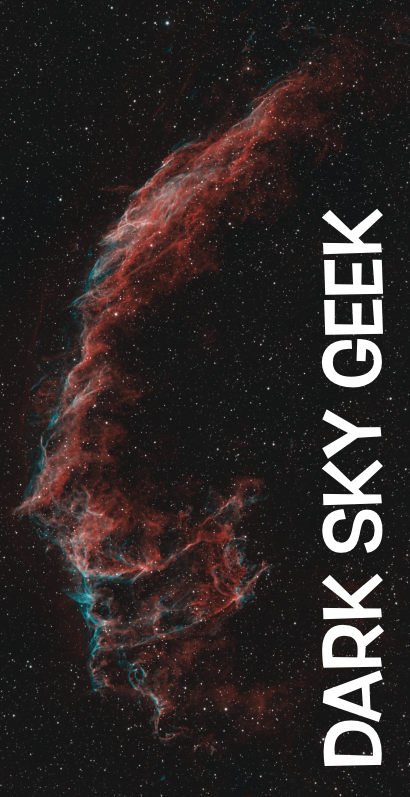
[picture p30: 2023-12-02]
Installer/WizardImageFile.bmp

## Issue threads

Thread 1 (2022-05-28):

EEPROM.h: No such file or directory

OriomMao, 2022-05-28:
I use Seeeduino XIAO，upload the code，it show：
`Arduino:1.8.19 (Windows Store 1.8.57.0) (Windows 10), 开发板："Seeeduino XIAO, Arduino, Off, USART"

Arduino_Firmware:11:10: fatal error: EEPROM.h: No such file or directory

compilation terminated.

exit status 1

EEPROM.h: No such file or directory

在文件 -> 首选项开启
“编译过程中显示详细输出”选项
这份报告会包含更多信息。
`
Then I use Arduino uno， it‘s OK

jlecomte, 2022-05-28:
Interesting! Indeed, it seems like the Seeeduino Xiao does not have any EEPROM. I have a few units myself but had not yet tried on them (so far, I've been developing the firmware using an Uno clone) But it seems like there are several options:

1. Option #1 is to not use EEPROM. All the EEPROM-related code would be in `#ifdef ... #endif` blocks... This is not so great because you lose the ability to remember the position of the focuser during a power cycle, which is kind of important.
2. Option #2 is to use something like this: https://github.com/khoih-prog/FlashStorage_SAMD. Unfortunately, this also has a downside. The number of writes will be limited to about 10,000 times. Once you get in that neighborhood, your chip is dead.
3. Option #3 is to use a separate EEPROM chip and use that instead of relying on the micro-controller.
4. Option #4 is to not use a Xiao. I love that little microcontroller board, but for this application, maybe it's not ideal. I am going to experiment with an ATTiny85 board to see if it works well. I will update the README accordingly.

Any other idea @OriomMao ?

jlecomte, 2022-05-29:
I updated the README to warn people of this compatibility issue and to let them know what to do. See https://github.com/jlecomte/ascom-oag-focuser/#microcontroller-compatibility

Closed 2022-05-29.

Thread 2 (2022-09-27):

ASCOM.DarkSkyGeek.OAGFocusDriver.dll

JoeBleau1, 2022-09-27:
Hello, I'm not able to register to my windows 10 pc the ASCOM.DarkSkyGeek.OAGFocusDriver.dll.
I follow the steps indicated but always end with the same message. I even created the dll with visual studio whitout any troubles, but I try to register the dll and those messages appear:

RegAsm : warning RA0000 : Registering an unsigned assembly with /codebase can cause your assembly to interfere with other applications that may be installed on the same computer. The /codebase switch is intended to be used only with signed assemblies. Please give your assembly a strong name and re-register it.
RegAsm : error RA0000 : An error occurred inside the user defined Register/Unregister functions: System.TypeInitializationException: The type initializer for 'ASCOM.DarkSkyGeek.FilterWheelProxy' threw an exception. ---> System.FormatException: Input string was not in a correct format.
   at System.Number.StringToNumber(String str, NumberStyles options, NumberBuffer& number, NumberFormatInfo info, Boolean parseDecimal)
   at System.Number.ParseDecimal(String value, NumberStyles options, NumberFormatInfo numfmt)
   at System.Convert.ToDecimal(String value)
   at ASCOM.DarkSkyGeek.FilterWheelProxy..cctor()
   --- End of inner exception stack trace ---
   at ASCOM.DarkSkyGeek.FilterWheelProxy.RegUnregASCOM(Boolean bRegister)

 I looked at the RA0000 error on the net but this went in a spiral of wouldbe solutions...

Is there a simple solution to this issue ?

Best regards

jlecomte, 2022-09-27:
See **step 2** in https://github.com/jlecomte/ascom-oag-focuser#downloading-and-installing-the-driver. Are you running the command prompt (`cmd.exe`) **as an administrator**?

JoeBleau1, 2022-09-27:
Yes I run the cmd.exe as administrator.

jlecomte, 2022-09-27:
ok, I know what's causing it! It's this line:
https://github.com/jlecomte/ascom-oag-focuser/blob/master/ASCOM_Driver/FilterWheelProxyDriver.cs#L76

Alright, I'll fix it tonight and publish a new release. Thank you for letting me know!

JoeBleau1, 2022-09-27:
You are so cool !
Thank's

jlecomte, 2022-09-28:
OK, please try using the files published in release `v1.0.2`: https://github.com/jlecomte/ascom-oag-focuser/releases/tag/v1.0.2

JoeBleau1, 2022-09-28:
Just did. Still not working, here is the output messages.
**************
RegAsm : warning RA0000 : Registering an unsigned assembly with /codebase can cause your assembly to interfere with other applications that may be installed on the same computer. The /codebase switch is intended to be used only with signed assemblies. Please give your assembly a strong name and re-register it.
RegAsm : error RA0000 : An error occurred inside the user defined Register/Unregister functions: System.TypeInitializationException: The type initializer for 'ASCOM.DarkSkyGeek.FilterWheelProxy' threw an exception. ---> System.FormatException: Input string was not in a correct format.
   at System.Number.StringToNumber(String str, NumberStyles options, NumberBuffer& number, NumberFormatInfo info, Boolean parseDecimal)
   at System.Number.ParseDecimal(String value, NumberStyles options, NumberFormatInfo numfmt)
   at System.Convert.ToDecimal(String value)
   at ASCOM.DarkSkyGeek.FilterWheelProxy..cctor()
   --- End of inner exception stack trace ---
   at ASCOM.DarkSkyGeek.FilterWheelProxy.RegUnregASCOM(Boolean bRegister)

jlecomte, 2022-09-28:
OK, one last try, if this one does not work, then I have no idea: https://github.com/jlecomte/ascom-oag-focuser/releases/tag/v1.0.3. Let me know! Thanks.

JoeBleau1, 2022-09-28:
Julien,
Bravo ! It worked, the dll is now registered.
I can now connect the app, and go to settings etc...
Thank you very much.

JoeBleau1, 2022-09-28:
Have a great evening.
Best regards.

jlecomte, 2022-09-28:
Brilliant! Thanks for the bug report :)

JoeBleau1, 2022-09-28:
Julien you are more then welcome. :)

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

Closed 2022-09-28.

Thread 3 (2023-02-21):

Do you think I can be successful?

Wellco, 2023-02-21:
Hi Julien, I would love to give this project a go, but I have a few concerns mostly around my ability. I will need to modify the 3D files as I have an Antia focuser, OAG and filter draw, not the ZWO. I have zero skills in FreeCAD, but have decided to use Fusion 360 as I think that might be easier. I have already made some basic edits. The Antila is a touch bigger than the ZWO. I don't have a 3D printer, but will get the parts professionally printed. My next issue is the electronics where my knowledge is at an absolute zero. I would have to follow the information in here on GitHub verbatim. There would be no way for me to stray form the path. If I could not get the exact same components I would most likely be lost. However I would really like to see how far I can get. Would you be willing to help me if I get stuck?

Lastly should I hold on for the revised focuser with that battery, of should I crack on with the original design, as documented here on GitHub.

Thanks so much for sharing your wonderful project and knowledge here.

Tim CORSO

jlecomte, 2023-02-21:
Hi Tim,

Let me summarize:

1) Your equipment differs from the one for which this project was originally designed for.
2) You don't have much (any?) experience with 3D modeling.
3) You don't own a 3D printer.
4) You don't know anything about electronics, nor have the equipment needed to complete an electronics project.

So, to your question "will I be successful?", the answer is an unequivocal no, unfortunately.

To your other question "will I support you?", the answer is also no, unfortunately. I am willing to fix bugs or implement enhancements or answer questions, but I simply do not have the time to provide the full support that you would likely need to make progress on your project.

I hope this does not come out too harsh, but this answer will likely save you a bunch of time and frustration.

Maybe look at Pegasus Astro SCOPS OAG?

Wellco, 2023-02-21:
Hi Julien,

I appreciate your frank reply.

Points 1,2,3 are not really a problem, I worked for a CAD company most of my working life, just don't know FreeCAD or Fusion 360. The only part I would need to ask questions around would be the electronics and maybe some aspects of the software. I realise that you could answer a mountain of basic questions, and I wouldn't except that. May be there is more complexity to your project than meets my eye.

Pegasus solution is nice, but way to pricey for me at thus time. I may still have a go and see where I can get to. I may fail, but it will keep me amused while the clouds are paying a visit.

Thanks again

Tim

Closed 2023-02-21.

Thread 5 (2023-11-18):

Scops OAG: access to COM7 denied

mrnother, 2023-11-18:
Hello,
I know from the doc and the video, that the app should work fine with a Pegasus Astro "Scops" motorized OAG, too.
Unfortunately I have an issue here. Ascom Driver were registered without issues and I know that the OAG works on port COM7. When trying to connect to the device with the DarkSkyGeek app, I receive an error: "An error occured while connecting to the focuser".
I see the issue in the Ascom log, where it says that "access denied opening COM7" and also the Ascom Diagnostic tool says "accees to port COM7 got denied". Any ideas how I can fix this and find out more about the root cause?
Best,
Chris

jlecomte, 2023-11-19:
This is a generic problem not related to this driver. Something else must be using that port. Use the netstat command to find out.

Closed 2023-11-19.

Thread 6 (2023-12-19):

unhandled exception in focuser app

CheekyMonkey, 2023-12-19:
Hi Julien

There is a condition in the focuser app that will give an unhandled exception

The maximum target position of the focuser is 4000
Entering a number for the target position greater than 4000 will give an unhandled exception.

See below:

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

By the way, cool project. I made a focuser, but I made a no-solder version :)

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

jlecomte, 2023-12-19:
This is 100% normal and expected. If you want to go beyond 4000 steps, you have to update the maximum position in the driver settings dialog. 4000 is just the default value... I also recommend setting the zero position first. See https://www.youtube.com/watch?v=zPPIgVuxk4Y for more details.

CheekyMonkey, 2023-12-19:
> This is 100% normal and expected. If you want to go beyond 4000 steps, you have to update the maximum position in the driver settings dialog. 4000 is just the default value... I also recommend setting the zero position first. See https://www.youtube.com/watch?v=zPPIgVuxk4Y for more details.

Ah, thanks.
I need to read the manual :)

Closed 2023-12-19.

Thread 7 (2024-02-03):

What's the value of the capacitor on the PCB?

MDSchechtman, 2024-02-03:
I couldn't find the value for the capacitor shown on the PCB schematics and final assembly anywhere.

The small disk capacitor on one of my ULN2003 driver boards measured at 0.01uf but I see you're using an electrolytic which I can only find starting at 0.1uf.

jlecomte, 2024-02-03:
It’s a bulk capacitor. 10uF works fine.

jlecomte, 2024-02-03:
I will add that info to the README, I thought it was already there, somewhere.

MDSchechtman, 2024-02-03:
Great, thank you!

Closed 2024-02-03.

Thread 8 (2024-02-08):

Which version of Arduino IDE to compile/upload sketch?  Problem compiling with V2.3.0

Endymion42, 2024-02-08:
When I try to compile the sketch I get the following error message in the unmodified sketch:

/ascom-oag-focuser-2/Arduino_Firmware/Arduino_Firmware.ino:17:16: error: 'constexpr const auto OK' redeclared as different kind of symbol
 constexpr auto OK = "OK";

Which version of IDE do you compile with?  What platform? (I'm on MAC).

Thanks for any help and this cool focuser.

Endymion42, 2024-02-08:
I just installed V2.3.0 on windows and it successfully compiled the sketch without error so it appears to be an issue with the Arduinio IDE on Mac.  Closing issue.

Endymion42, 2024-02-08:
Closed

Closed 2024-02-08.

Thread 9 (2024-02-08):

Confused about hole sizes in base and cover

Endymion42, 2024-02-08:
I'm confused about the hole sizes in the base and cover.  The base holes are significantly smaller than the 4 mount holes in the cover.  As the bolt/screw needs to go through the base into the cover, how is this supposed to work?

Thanks for any help.  In the mean time I will use a feature in my slicer to fill in the cover holes and replace with smaller diameter holes.

jlecomte, 2024-02-09:
That is because the large holes are designed to host brass inserts. Please see the BOM. Thanks!

Endymion42, 2024-02-09:
Thank you for resolving my confusion.   Apologies, I looked around for a BOM but didn't see one listing the brass inserts.   Is it inside the FreeCad files or KiCad files somewhere?

jlecomte, 2024-02-09:
OK, I forgot to list that in the BOM. Sorry.

jlecomte, 2024-02-09:
Fixed in [this commit](https://github.com/jlecomte/ascom-oag-focuser/commit/b9ac257cc9738d94fbbac5315695e74b7e7cab98). Thanks!

Closed 2024-02-09.

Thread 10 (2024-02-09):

Notes on Celestron OAG Dimensions

Endymion42, 2024-02-09:
Attached are some notes on the critical dimensions of the Celestron OAG should you decide at some point to make a design for it.

[Notes on Celestron OAG Dimensions for ASCOM-OAG-FOCUSER Picture 1 .pdf](https://github.com/jlecomte/ascom-oag-focuser/files/14216520/Notes.on.Celestron.OAG.Dimensions.for.ASCOM-OAG-FOCUSER.Picture.1.pdf)
[Notes on Celestron OAG Dimensions for ASCOM-OAG-FOCUSER Picture 2 .pdf](https://github.com/jlecomte/ascom-oag-focuser/files/14216521/Notes.on.Celestron.OAG.Dimensions.for.ASCOM-OAG-FOCUSER.Picture.2.pdf)

jlecomte, 2024-02-23:
I will not support the Celestron OAG. I added a section to the README that documents OAG compatibility. Thanks!

Endymion42, 2024-02-26:
Here's a completed design for the Celestron OAG.   If acceptable, would you add it to your project for people who want to print and use it themselves?

Regards,
John

[CelestronOAG.zip](https://github.com/jlecomte/ascom-oag-focuser/files/14412291/CelestronOAG.zip)
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

Endymion42, 2024-02-26:
https://github.com/jlecomte/ascom-oag-focuser/assets/92014533/0007f066-bc40-46ed-a3a4-cc8e99c39e2c

Video in action.

jlecomte, 2024-02-27:
This is great! I see you attached an OpenSCAD file. Let me see if I can import it in FreeCAD. Thanks!

Endymion42, 2024-02-27:
OpenSCAD file is a bit messy - this may help:

BaseA is
rotate([180,0,0])
CelestronBaseA();

BaseB is
rotate([180,0,0])
CelestronBaseB();

Cover Plate is
TopCover();

Gear (60 teeth) is
CelestronGear();

Pinion (16 teeth) is
MotorPinion();

jlecomte, 2024-02-27:
I added the files to the GitHub repository, and credited you for this contribution. Thank you!

Endymion42, 2024-02-27:
Notes on printing the Celestron OAG parts.

I used 0.2mm with 15% fill.   No supports used on any parts but I do recommend a brim around BaseB as there is a possibility for the print to mess up at the end of the semicircular clamp if you don't.

Closed 2024-02-23.

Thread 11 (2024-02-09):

ULN2003A wrong way in fitzing schematic image

MDSchechtman, 2024-02-09:
The ULN2003A is actually backwards in the schematic, which threw me for a loop for a few minutes.

jlecomte, 2024-02-23:
Fixed in https://github.com/jlecomte/ascom-oag-focuser/pull/12. Thanks!

Closed 2024-02-23.

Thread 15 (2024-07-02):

Arduino_Firmware.ino compile warning

dlkeng, 2024-07-02:
When compiling Arduino_Firmware.ino for an Arduino Nano, the following warning occurs:
```
Arduino_Firmware.ino:71:42: warning: large integer implicitly truncated to unsigned type [-Woverflow]
 const unsigned int EEPROM_MAGIC_NUMBER = 0x12345678;
```
This appears to be due to trying to assign a 32-bit value to a 16-bit variable.

jlecomte, 2024-07-02:
Actually, fixing this requires changing a few more lines because `EEPROM.get` returns an `int`. For now, you can ignore the warning. I will fix this when I get the chance. Thanks!

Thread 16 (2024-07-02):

ASCOM Conform and ConformU errors and issues with DarkSkyGeek's OAG Focuser ASCOM driver

dlkeng, 2024-07-02:
Using the ASCOM **Conform** tool with the DarkSkyGeek's OAG Focuser ASCOM driver, the following error occurs:
```
11:06:06.354 SupportedActions   ERROR    Actions must be strings. The type of action 1 1 is: Int32

Your driver had 1 error, 0 warnings and 0 issues
```

Using the ASCOM **ConformU** tool with the DarkSkyGeek's OAG Focuser ASCOM driver, the following issues occur:
```
11:01:34.326 SupportedActions   ISSUE    Unexpected error: Specified cast is not valid.
11:01:34.329 SupportedActions   ISSUE    Specified cast is not valid.

11:01:40.697 Issue Summary       
11:01:40.699 SupportedActions   ISSUE    Unexpected error: Specified cast is not valid.
11:01:40.701 SupportedActions   ISSUE    Specified cast is not valid.
```

[Conform Log.txt](https://github.com/user-attachments/files/16071560/Conform.Log.txt)
[ConformU Log.txt](https://github.com/user-attachments/files/16071563/ConformU.Log.txt)

jlecomte, 2024-07-02:
Indeed, there is a small bug in the driver code. I'll fix it. Thanks for reporting!

jlecomte, 2024-07-02:
Fixed in release 1.3.1. Thanks!

Closed 2024-07-02.

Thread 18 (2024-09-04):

Adapter for ZWO OAG-L

naavis, 2024-09-04:
Hi! I'm sorry if this is a dumb question, but could you clarify what the [adapter piece](https://github.com/jlecomte/ascom-oag-focuser/blob/v2/3D_Files/ZWO-OAG-L/STL/Adapter.stl) is needed for when using the OAG motor focuser with the ZWO OAG-L? I printed the parts and am currently assembling them and putting the electronics together. My OAG is at the local observatory in active remote imaging use, so I don't have it at hand now. Maybe the need for the adapter becomes clear when I actually go install the focuser parts, but it would be nice to understand ahead of time what the adapter is for.

Judging by the shape and threading, does it somehow go between the OAG prism and the 1.25" helical focuser?

jlecomte, 2024-09-04:
For ZWO OAG-L, you can either make the custom designed version, in which case you won’t need an adapter, or you can make the standard version and use the adapter to fit the ZWO helical focuser (M42 female thread)  to the ZWO OAG-L body (4 tiny screws)

naavis, 2024-09-04:
I am not sure I entirely follow. The OAG-L comes with a helical focuser attached. Why would I need the printed adapter?

jlecomte, 2024-09-04:
Exactly! You don’t need the adapter. The reason I created the adapter is for people who might own multiple different OAGs and they want to swap the focuser between those OAGs. During the crowdfunding campaign, I had several such requests.

naavis, 2024-09-05:
Alright, thanks for the clarification. And great project! Solves exactly the problem I've been having a while with my imaging setup.

Closed 2024-09-04.

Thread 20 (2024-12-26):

Two instances of ASCOM Focuser Driver

pengsloth, 2024-12-26:
After seeing your video I was intrigued of using this ASCOM driver not only for adjusting focus of an OAG but also the camera itself.

Voyager is an amazing automation software however the developer refuses to add the ability to do filter offsets. Using your driver also an external use of filter offsets that is transparent to Voyager which is wonderful!

My question is, since I'm using this with the main filter wheel and main camera focuser could I set up a second instance to also operate the OAG focuser.

So the main filter wheel changes from Lum to Ha which changes the main focuser by -140 steps as well as changes the OAG focuser by say 80 steps.

jlecomte, 2024-12-31:
You cannot have 2 instances of the ASCOM focuser driver running at the same time on a PC. You need to use two separate PCs.

pengsloth, 2024-12-31:
Would it be possible then to have both the main camera focuser and the OAG focuser available in the Proxy driver? So when a filter is changed it would adjust the main camera focus (technically NINA can do this already but Voyager won't add the ability) and also adjust the focus of the OAG to match the change?

jlecomte, 2024-12-31:
No, it would not be possible. May I recommend you switch to NINA? :)

Closed 2024-12-31.

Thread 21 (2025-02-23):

Patch to support Xiao RP2040 Board & other RP2040 boards

michael-ring, 2025-02-23:
This project:

https://github.com/earlephilhower/arduino-pico

adds arduino support to a huge number of rp2040 boards. In my case I used the XIAO RP2040 board.

The library brings support for EEPROM, however, support has to be initialized first.

Do do so, this patch can be applied:

diff --git a/Arduino_Firmware/Arduino_Firmware.ino b/Arduino_Firmware/Arduino_Firmware.ino
index 2536676..053b05d 100644
--- a/Arduino_Firmware/Arduino_Firmware.ino
+++ b/Arduino_Firmware/Arduino_Firmware.ino
@@ -109,6 +109,9 @@ void setup() {
     direction = forward;
     position = 0;
     last_step_time = 0L;
+    #if PICO_RP2040 == 1
+      EEPROM.begin(256);
+    #endif

     int magic_number;
     EEPROM.get(EEPROM_MAGIC_NUMBER_ADDR, magic_number);

jlecomte, 2025-02-23:
Please, open a pull request. That will make it a lot easier to review and merge. Only then can I close this issue. Thanks!

Closed 2025-03-28.

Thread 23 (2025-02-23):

Support for TMC2209 Chip

michael-ring, 2025-02-23:
I plan to implement support for the TMC2209 chip for the OAG focusser, reason is that there are two rather cheap boards:

https://makerbase3d.com/product/mks-thr36-thr42-board

that offer a complete solution without the need for any soldering.

Are you willing to accept a PR for my Codechanges once they are done?

Thanks,

Michael

jlecomte, 2025-02-23:
I am willing to review a pull request if you open one. Thanks!

Closed 2025-02-24.

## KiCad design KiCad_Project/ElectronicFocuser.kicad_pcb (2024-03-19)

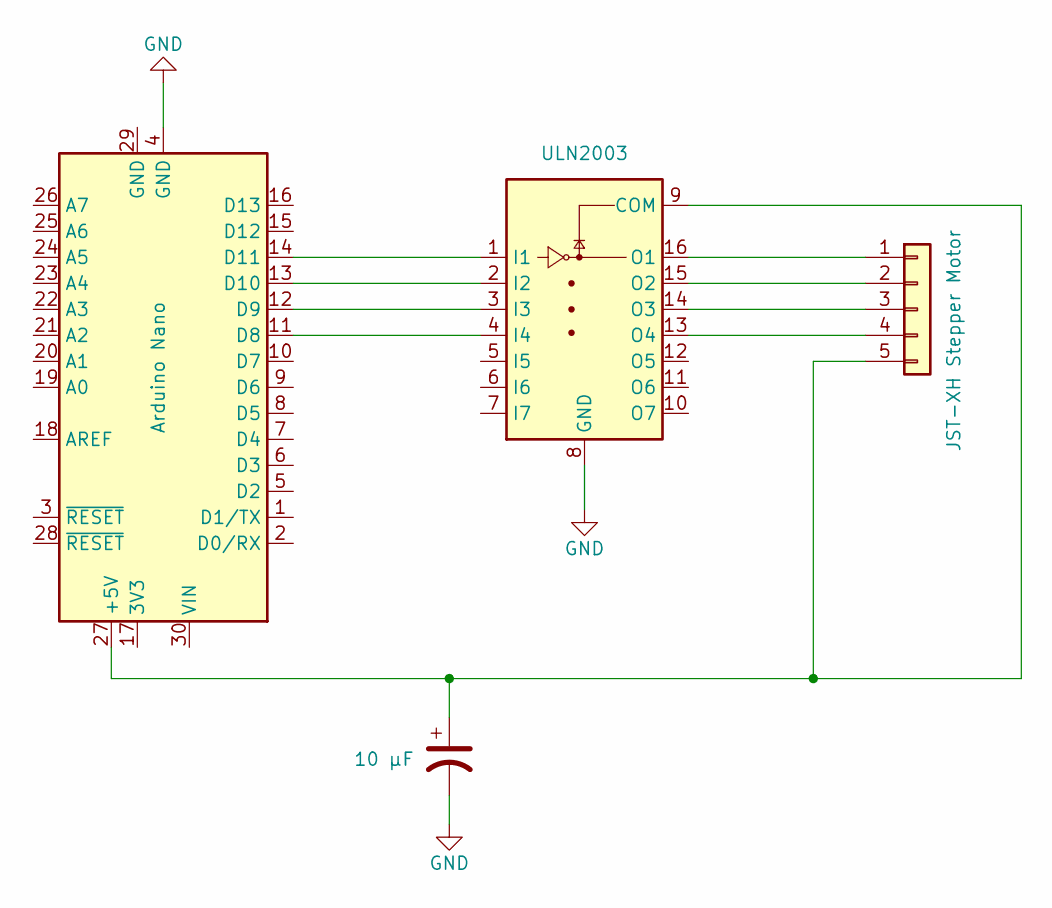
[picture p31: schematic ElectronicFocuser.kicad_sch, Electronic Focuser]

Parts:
A1: Arduino Nano; Arduino_Nano
C1: 10 µF; CP_Radial_D4.0mm_P2.00mm
J1: JST-XH Stepper Motor; JST_XH_B5B-XH-A_1x05_P2.50mm_Vertical
U1: ULN2003; DIP-16_W7.62mm

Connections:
GND: A1.4 (GND), C1.2, U1.8 (GND)
unnamed: A1.11 (D8), U1.4 (I4)
unnamed: A1.12 (D9), U1.3 (I3)
unnamed: A1.13 (D10), U1.2 (I2)
unnamed: A1.14 (D11), U1.1 (I1)
unnamed: A1.27 (+5V), C1.1, J1.5, U1.9 (COM)
unnamed: J1.1, U1.16 (O1)
unnamed: J1.2, U1.15 (O2)
unnamed: J1.3, U1.14 (O3)
unnamed: J1.4, U1.13 (O4)

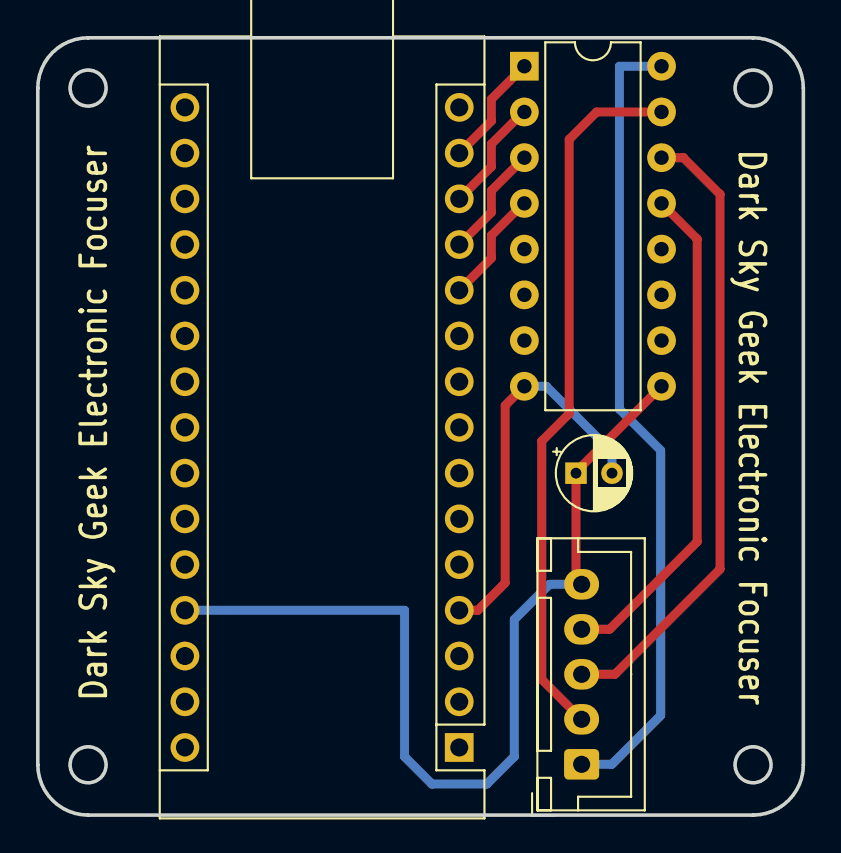
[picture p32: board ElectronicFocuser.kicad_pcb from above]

Board: 2 copper layers, 42.5 x 43.2 mm, 4 parts (0 on the bottom side), 10 nets.

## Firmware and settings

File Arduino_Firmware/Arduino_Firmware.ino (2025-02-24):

/*
 * Arduino_Firmware.ino
 * Copyright (C) 2022 - Present, Julien Lecomte - All Rights Reserved
 * Licensed under the MIT License. See the accompanying LICENSE file for terms.
 */

// Note that I don't use the standard Arduino stepper library because I need
// to be able to respond to commands while the motor is moving, so I manually
// move the stepper motor 1 step at a time.

#include <EEPROM.h>

//-- CONSTANTS ----------------------------------------------------------------

constexpr auto DEVICE_GUID = "6e18ce4b-0d7b-4850-8470-80df623bf0a4";

constexpr auto OK = "OK";
constexpr auto NOK = "NOK";

constexpr auto TRUE = "TRUE";
constexpr auto FALSE = "FALSE";

constexpr auto COMMAND_PING = "COMMAND:PING";
constexpr auto RESULT_PING = "RESULT:PING:OK:";

constexpr auto COMMAND_INFO = "COMMAND:INFO";
constexpr auto RESULT_INFO = "RESULT:INFO:DarkSkyGeek's OAG Focuser Firmware v1.0";

constexpr auto COMMAND_FOCUSER_GETPOSITION = "COMMAND:FOCUSER:GETPOSITION";
constexpr auto RESULT_FOCUSER_POSITION = "RESULT:FOCUSER:POSITION:";

constexpr auto COMMAND_FOCUSER_ISMOVING = "COMMAND:FOCUSER:ISMOVING";
constexpr auto RESULT_FOCUSER_ISMOVING = "RESULT:FOCUSER:ISMOVING:";

constexpr auto COMMAND_FOCUSER_SETZEROPOSITION = "COMMAND:FOCUSER:SETZEROPOSITION";
constexpr auto RESULT_FOCUSER_SETZEROPOSITION = "RESULT:FOCUSER:SETZEROPOSITION:";

constexpr auto COMMAND_FOCUSER_MOVE = "COMMAND:FOCUSER:MOVE:";
constexpr auto RESULT_FOCUSER_MOVE = "RESULT:FOCUSER:MOVE:";

constexpr auto COMMAND_FOCUSER_HALT = "COMMAND:FOCUSER:HALT";
constexpr auto RESULT_FOCUSER_HALT = "RESULT:FOCUSER:HALT:";

constexpr auto ERROR_INVALID_COMMAND = "ERROR:INVALID_COMMAND";

// According to the data sheet, when the 28BYJ-48 motor runs in full step mode,
// each step corresponds to a rotation of 11.25°. That means there are 32 steps
// per revolution. Additionally, the motor is outfitted with a gearbox that has
// a ratio of 64:1, which means that a full revolution requires 2,048 steps.
const unsigned int STEPS_PER_REVOLUTION = 2048;

// The ZWO helical focuser moves only over about a 220° range.
// The gear ratio between small pulley and the focuser body is roughly 1:4.
// Therefore, we set MAX_STEPS at 5,000 steps.
const unsigned int MAX_STEPS = 5000;

// 6RPM = 1 revolution of the motor axle takes 10 seconds.
// No need to go crazy fast (stepper motors lose torque at higher speeds),
// and no need to go crazy slow. This value seems like a happy medium...
const unsigned int RPM_SPEED = 6;

// How long do we wait between each step in order to achieve the desired speed?
const unsigned long STEP_DELAY_MICROSEC = (60L * 1000L * 1000L) / (STEPS_PER_REVOLUTION * RPM_SPEED);

// Pins controlling the motor. Change this depending on your exact wiring!
const unsigned int MOTOR_PIN_1 = 11; // Blue   - 28BYJ48 pin 1
const unsigned int MOTOR_PIN_2 =  9; // Yellow - 28BYJ48 pin 3
const unsigned int MOTOR_PIN_3 = 10; // Pink   - 28BYJ48 pin 2
const unsigned int MOTOR_PIN_4 =  8; // Orange - 28BYJ48 pin 4

const unsigned int EEPROM_MAGIC_NUMBER = 0x12345678;
const unsigned int EEPROM_MAGIC_NUMBER_ADDR = 0;
const unsigned int EEPROM_POSITION_BASE_ADDR = 4;

//-- VARIABLES ----------------------------------------------------------------

// While moving, steps_left > 0
// When not moving, steps_left == 0
int steps_left;

enum Direction {
    forward = 1,
    backward = -1
} direction;

// The current position, which we store in EEPROM
int position;

unsigned long last_step_time;

//-- MICROCONTROLLER FUNCTIONS ------------------------------------------------

// The `setup` function runs once when you press reset or power the board.
void setup() {
    // Initialize serial port I/O.
    Serial.begin(57600);
    while (!Serial) {
        ; // Wait for serial port to connect. Required for native USB!
    }
    Serial.flush();

    // Initialize motor control pins...
    pinMode(MOTOR_PIN_1, OUTPUT);
    pinMode(MOTOR_PIN_2, OUTPUT);
    pinMode(MOTOR_PIN_3, OUTPUT);
    pinMode(MOTOR_PIN_4, OUTPUT);

    steps_left = 0;
    direction = forward;
    position = 0;
    last_step_time = 0L;
    
    #if PICO_RP2040 == 1
        EEPROM.begin(256);
    #endif

    int magic_number;
    EEPROM.get(EEPROM_MAGIC_NUMBER_ADDR, magic_number);
    if (magic_number == EEPROM_MAGIC_NUMBER) {
        // The value stored in EEPROM is trustworthy...
        EEPROM.get(EEPROM_POSITION_BASE_ADDR, position);
    } else {
        // The position had never been stored in EEPROM. Initialize it to 0...
        position = 0;
        // Store it...
        EEPROM.put(EEPROM_POSITION_BASE_ADDR, position);
        // And mark the value as trustworthy...
        EEPROM.put(EEPROM_MAGIC_NUMBER_ADDR, EEPROM_MAGIC_NUMBER);
    }
}

// The `loop` function runs over and over again until power down or reset.
void loop() {
    if (Serial.available() > 0) {
        String command = Serial.readStringUntil('\n');
	command.replace("\r","");
        if (command == COMMAND_PING) {
            handlePing();
        }
        else if (command == COMMAND_INFO) {
            sendFirmwareInfo();
        }
        else if (command == COMMAND_FOCUSER_ISMOVING) {
            sendFocuserState();
        }
        else if (command == COMMAND_FOCUSER_GETPOSITION) {
            sendFocuserPosition();
        }
        else if (command == COMMAND_FOCUSER_SETZEROPOSITION) {
            setFocuserZeroPosition();
        }
        else if (command.startsWith(COMMAND_FOCUSER_MOVE)) {
            String arg = command.substring(strlen(COMMAND_FOCUSER_MOVE));
            int value = arg.toInt();
            moveFocuser(value);
        }
        else if (command == COMMAND_FOCUSER_HALT) {
            haltFocuser();
        }
        else {
            handleInvalidCommand();
        }
    }

    // Make the stepper motor move, if needed, 1 step at a time...
    step();
}

//-- UTILITY FUNCTIONS -----------------------------------------------------

// See https://forum.arduino.cc/t/modulo-with-negative-int/158317
int mod(int x, int y){
    return x < 0 ? ((x+1) % y) + y - 1 : x % y;
}

void step() {
    if (steps_left > 0) {
        // Make sure we don't prematurely take a step if it's too early...
        unsigned long now = micros();
        if (now - last_step_time < STEP_DELAY_MICROSEC) {
            return;
        }

        last_step_time = now;

        steps_left--;

        if (direction == forward) {
            position++;
        } else {
            position--;
        }

        switch (mod(position, 4)) {
            case 0: // 1010
                digitalWrite(MOTOR_PIN_1, HIGH);
                digitalWrite(MOTOR_PIN_2, LOW);
                digitalWrite(MOTOR_PIN_3, HIGH);
                digitalWrite(MOTOR_PIN_4, LOW);
                break;
            case 1: // 0110
                digitalWrite(MOTOR_PIN_1, LOW);
                digitalWrite(MOTOR_PIN_2, HIGH);
                digitalWrite(MOTOR_PIN_3, HIGH);
                digitalWrite(MOTOR_PIN_4, LOW);
                break;
            case 2: // 0101
                digitalWrite(MOTOR_PIN_1, LOW);
                digitalWrite(MOTOR_PIN_2, HIGH);
                digitalWrite(MOTOR_PIN_3, LOW);
                digitalWrite(MOTOR_PIN_4, HIGH);
                break;
            case 3: // 1001
                digitalWrite(MOTOR_PIN_1, HIGH);
                digitalWrite(MOTOR_PIN_2, LOW);
                digitalWrite(MOTOR_PIN_3, LOW);
                digitalWrite(MOTOR_PIN_4, HIGH);
                break;
        }

        if (steps_left == 0) {
            stop();
        }
    }
}

void stop() {
    // Make sure we don't take another step.
    steps_left = 0;

    // Store the final position in EEPROM.
    EEPROM.put(EEPROM_POSITION_BASE_ADDR, position);

    // And de-energize the stepper by setting all the pins to LOW to save power,
    // prevent heat build up, and eliminate vibrations.
    digitalWrite(MOTOR_PIN_1, LOW);
    digitalWrite(MOTOR_PIN_2, LOW);
    digitalWrite(MOTOR_PIN_3, LOW);
    digitalWrite(MOTOR_PIN_4, LOW);
}

//-- FOCUSER HANDLING ------------------------------------------------------

void sendFocuserState() {
    Serial.print(RESULT_FOCUSER_ISMOVING);
    Serial.println(steps_left != 0 ? TRUE : FALSE);
}

void sendFocuserPosition() {
    Serial.print(RESULT_FOCUSER_POSITION);
    Serial.println(position);
}

void setFocuserZeroPosition() {
    Serial.print(RESULT_FOCUSER_SETZEROPOSITION);
    if (steps_left == 0) {
        position = 0;
        EEPROM.put(EEPROM_POSITION_BASE_ADDR, position);
        Serial.println(OK);
    } else {
        // Cannot set zero position while focuser is still moving...
        Serial.println(NOK);
    }
}

void moveFocuser(int target_position) {
    Serial.print(RESULT_FOCUSER_MOVE);

    if (steps_left > 0) {
        // Cannot move while focuser is still moving from previous request...
        Serial.println(NOK);
        return;
    }

    steps_left = abs(target_position - position);

    if (target_position >= position) {
        direction = forward;
    } else {
        direction = backward;
    }

    Serial.println(OK);
}

void haltFocuser() {
    stop();
    Serial.print(RESULT_FOCUSER_HALT);
    Serial.println(OK);
}

//-- MISCELLANEOUS ------------------------------------------------------------

void handlePing() {
    Serial.print(RESULT_PING);
    Serial.println(DEVICE_GUID);
}

void sendFirmwareInfo() {
    Serial.println(RESULT_INFO);
}

void handleInvalidCommand() {
    Serial.println(ERROR_INVALID_COMMAND);
}

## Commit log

2022-05-22 Fixed initial set of bugs
    [Arduino_Firmware.ino]
2022-05-23 Fix heat build up by powering off the stepper when idle
    [Arduino_Firmware.ino]
2022-05-23 Code cleanup + added backlash handling and leveraged step ratio
2022-05-24 Added first 3D files
    [ZWO_OAG_Focuser_Pulley.FCStd, ZWO_OAG_Focuser_Pulley.stl]
2022-05-25 Fixed lots and lots of small - and not so small - issues
    [Arduino_Firmware.ino]
2022-05-25 Small tweaks to make the driver work with scops OAG
2022-05-25 Added electronics schematics
    [Breadboard_Circuit.fzz]
2022-05-26 Fixed small routing issue in electronics schematics
    [Breadboard_Circuit.fzz]
2022-05-28 Allow focuser to reverse rotation due to gearing
    [Arduino_Firmware.ino]
2022-06-06 Added all necessary 3D files
    [Circuit_Board_Box.stl, Focuser_Body.FCStd, Focuser_Gears.FCStd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]
2022-06-16 Added calibration procedure
2023-12-15 Updated assets for v2
    [Breadboard_Circuit.fzz, ElectronicFocuser.kicad_pcb, ElectronicFocuser.kicad_sch]
2023-12-19 v2 WIP
    [Circuit_Board_Box.stl, Focuser_Body.FCStd, Focuser_Gear.stl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]
2023-12-31 Updated PCB layout to make room for attachments
    [ElectronicFocuser.kicad_pcb]
2023-12-31 Reshaped gears
    [Gear.stl, Gears.FCStd, Pinion.stl]
2024-01-05 Updated 3D model and printed gears images
    [Body.FCStd]
2024-01-06 Updated 3D model
    [Base.stl, Body.FCStd, Cover.stl]
2024-01-13 Updated 3D files
    [Base.stl, Body.FCStd, Cover.stl]
2024-02-23 OAG Compatibility + Fixes (#12)
    [Adapter.FCStd, Adapter.stl, Base.stl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]
2024-02-27 Added Celestron OAG model files contributed by Endymion42 - see issue #10
    [BaseA.stl, BaseB.stl, BodyAndGears.scad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]
2024-03-09 Update MainForm.cs (#13)
    Current version throws exception updating from non uni thread when clicking on the left and right arrows
2024-03-11 Fixed 3D model for standard version
    [Base.stl, Body.FCStd, Cover.stl]
2024-03-12 Small tweak to the 3D models
    [Base.stl, Body.FCStd, Cover.stl]
2024-03-16 Small tweak to the 3D model for better gear meshing
    [Base.stl, Body.FCStd]
2024-03-16 Tweak the gear to better fit the ZWO helical focuser
    [Gear.stl, Gears.FCStd]
2024-03-19 Forgot to connect pin 9 of ULN2003, which could cause electrical issues due to EMF
    [Breadboard_Circuit.fzz, ElectronicFocuser.kicad_pcb, ElectronicFocuser.kicad_sch]
2025-02-24 Support Xiao RP2040 Board & other RP2040 boards

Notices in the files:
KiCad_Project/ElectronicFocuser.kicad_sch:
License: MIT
